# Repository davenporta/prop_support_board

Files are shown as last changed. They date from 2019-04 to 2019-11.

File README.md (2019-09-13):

# Prop Support Board
Michigan Aeronautial Science Association

Alex Davenport

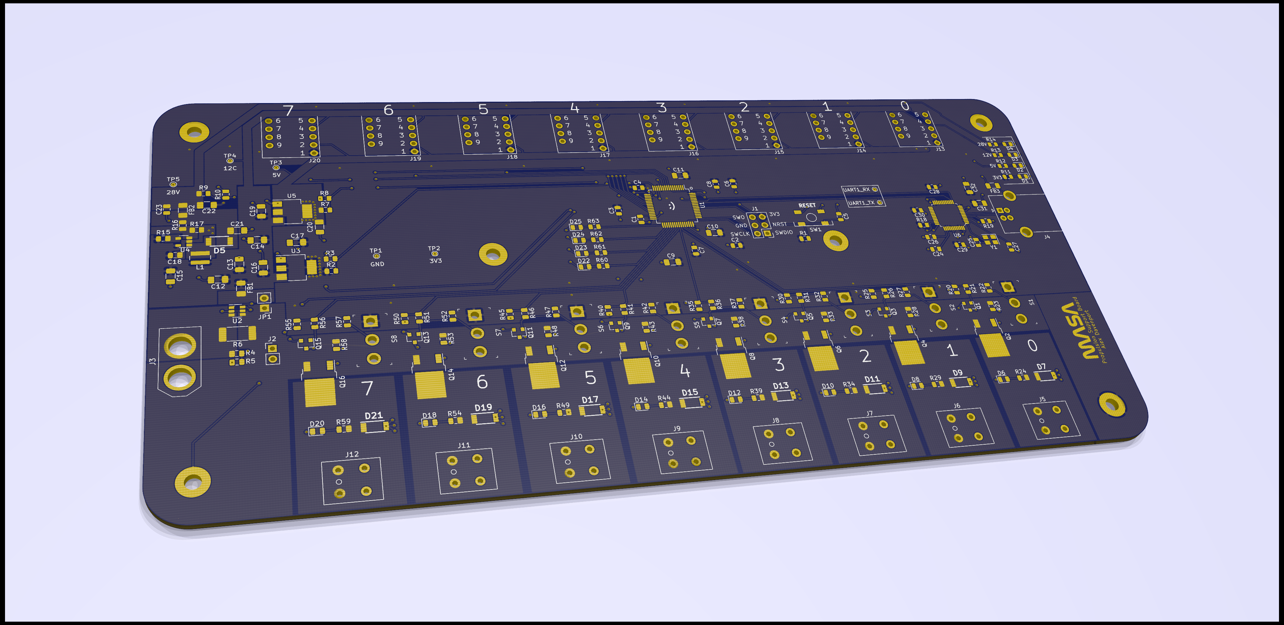
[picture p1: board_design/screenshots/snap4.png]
shiny


### Capabilities
* 8x 12V Solenoid Valve Channels
* 8x Configurable Sensor Channels

### Sensor Channels
* Analog signal out to MCU's integrated ADC
* 3.3V, 5V, 12V, and 28V supply
* Asymmetrical 9-pin header connector
* Configurable with 6 types of sensor conditioning "daughter" boards

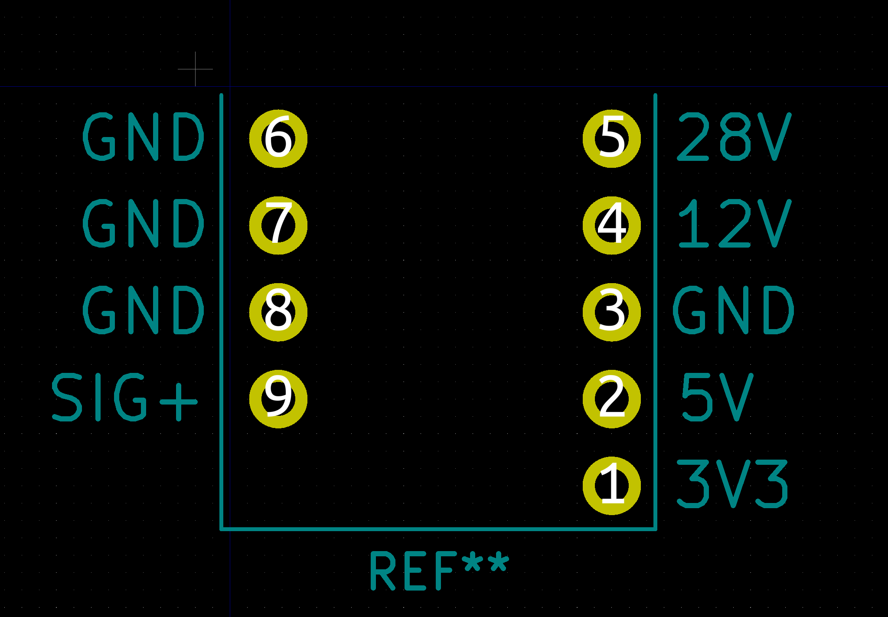
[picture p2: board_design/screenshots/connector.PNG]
asymmetrical!


### Available Sensor Boards
* 3-wire Pressure Transducer w/ configurable excitation
* 4-wire Pressure Transducer w/ configurable excitation (WIP)
* T or K-type Thermocouples
* Load Cells
* RTDs (WIP)
* Capacitive Level Sensor (WIP)

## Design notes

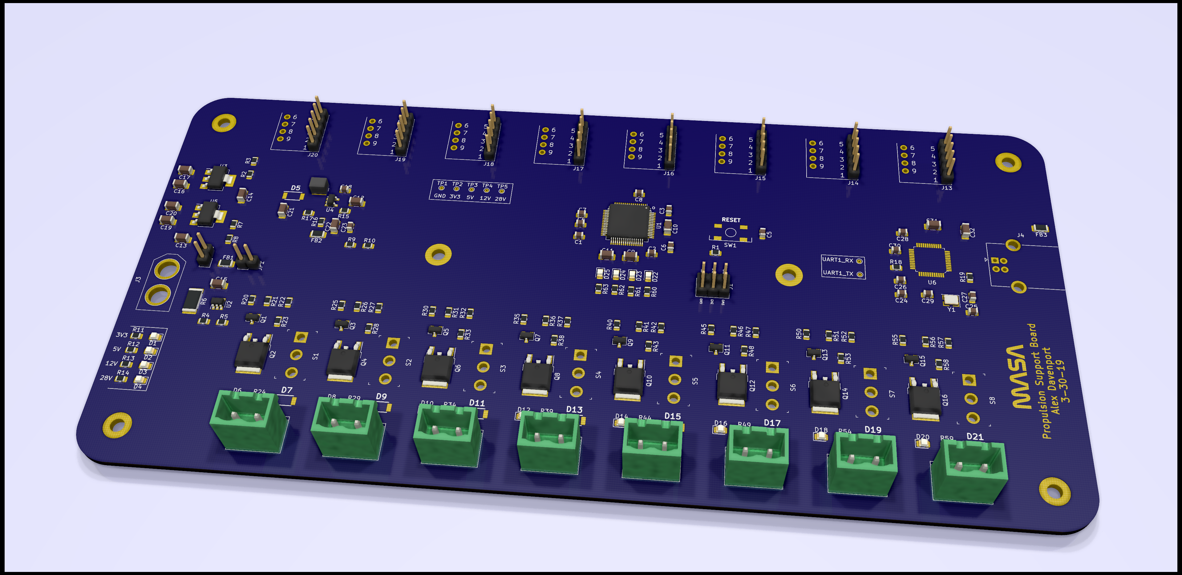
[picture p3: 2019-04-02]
board_design/screenshots/snap2.png

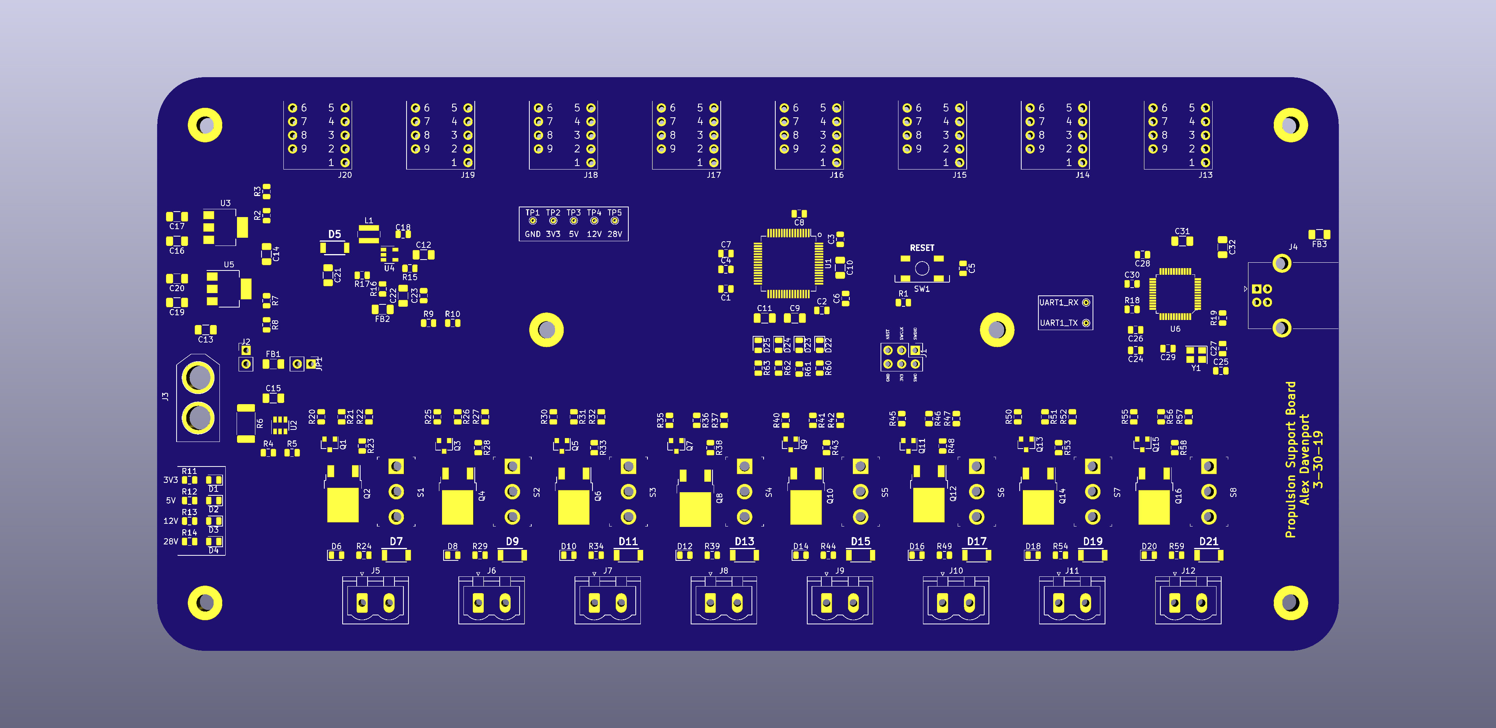
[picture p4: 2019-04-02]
board_design/screenshots/snap.png

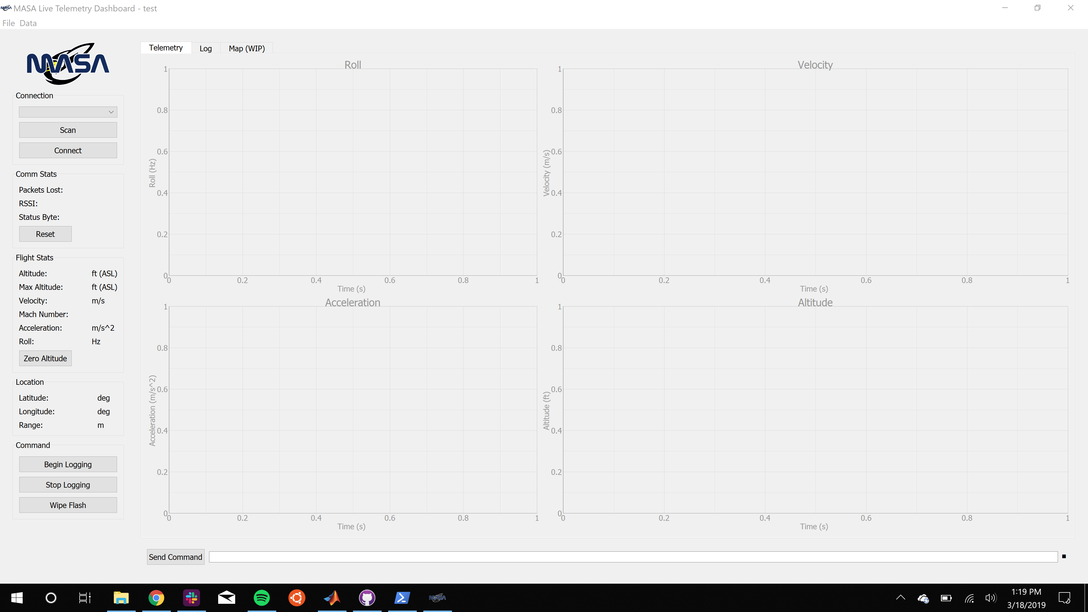
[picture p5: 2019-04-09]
gui/screenshot.png

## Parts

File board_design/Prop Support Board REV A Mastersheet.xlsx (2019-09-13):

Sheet: Pin Budget
ADC |  |  | GPIO
channel | pin | adc channel | channel | pin
ebatt | PA0 | ADC1_IN0 | en_vlv0 | PA11
ibus | PA1 | ADC1_IN1 | en_vlv1 | PA10
e3v3 | PA2 | ADC1_IN2 | en_vlv2 | PA9
e5v | PA3 | ADC1_IN3 | en_vlv3 | PA8
e28v | PA4 | ADC1_IN4 | en_vlv4 | PC9
sig0 | PA5 | ADC1_IN5 | en_vlv5 | PC8
sig1 | PA6 | ADC1_IN6 | en_vlv6 | PC7
sig2 | PA7 | ADC1_IN7 | en_vlv7 | PC6
sig3 | PB0 | ADC1_IN8 | LED_0 | PB12
sig4 | PB1 | ADC1_IN9 | LED_1 | PB13
sig5 | PC0 | ADC1_IN10 | LED_2 | PB14
sig6 | PC1 | ADC1_IN11 | LED_3 | PB15
sig7 | PC2 | ADC1_IN12

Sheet: Bill of Materials
Source: | C:\Users\alexh\OneDrive\Desktop\masa\prop_support_board\prop_support\prop_support.sch
Date: | 2019-03-30 15:33
Tool: | Eeschema (5.1.0)-1
Generator: | C:\Program Files\KiCad\bin\scripting\plugins/bom_csv_grouped_by_value.py
Component Count: | 183
Collated Components:
Item | Qty | Reference(s) | Value | LibPart | Footprint
1 | 2 | C1, C18 | 4u7 | Device:C | Capacitor_SMD:C_0805_2012Metric
2 | 13 | C2, C3, C4, C5, C6, C7, C8, C23, C24, C26, C28, C29, C30 | 100n | Device:C | Capacitor_SMD:C_0805_2012Metric
3 | 13 | C9, C10, C11, C12, C13, C14, C15, C16, C17, C19, C20, C21, C22 | 10u | Device:C | Capacitor_SMD:C_1206_3216Metric
4 | 2 | C25, C27 | 18p | Device:C | Capacitor_SMD:C_0805_2012Metric
5 | 2 | C31, C32 | 1u | Device:C | Capacitor_SMD:C_1206_3216Metric
6 | 16 | D1, D2, D3, D4, D6, D8, D10, D12, D14, D16, D18, D20, D22, D23, D24, D25 | LED | Device:LED | LED_SMD:LED_0805_2012Metric
7 | 1 | D5 | D_Schottky | Device:D_Schottky | davenport_kicad_footprints:SODFL4725X110N
8 | 8 | D7, D9, D11, D13, D15, D17, D19, D21 | D | Device:D | davenport_kicad_footprints:SODFL4725X110N
9 | 3 | FB1, FB2, FB3 | Ferrite_Bead | Device:Ferrite_Bead | Resistor_SMD:R_1206_3216Metric
10 | 6 | H1, H2, H3, H4, H5, H6 | MountingHole_Pad | Mechanical:MountingHole_Pad | MountingHole:MountingHole_3.2mm_M3_Pad
11 | 1 | J1 | Conn_02x03_Counter_Clockwise | Connector_Generic:Conn_02x03_Counter_Clockwise | Connector_PinHeader_1.00mm:PinHeader_2x03_P1.00mm_Vertical
12 | 1 | J2 | GS2 | Device:Jumper | Connector_PinHeader_1.00mm:PinHeader_1x02_P1.00mm_Vertical
13 | 1 | J3 | XT-60_female | davenport-kicad:XT-60_female | davenport_kicad_footprints:XT60
14 | 1 | J4 | USB_B | Connector:USB_B | Connector_USB:USB_B_OST_USB-B1HSxx_Horizontal
15 | 8 | J5, J6, J7, J8, J9, J10, J11, J12 | Screw_Terminal_01x02 | Connector:Screw_Terminal_01x02 | Connector_Phoenix_MSTB:PhoenixContact_MSTBVA_2,5_2-G_1x02_P5.00mm_Vertical
16 | 8 | J13, J14, J15, J16, J17, J18, J19, J20 | Conn_01x09_Female | Connector:Conn_01x09_Female | davenport_kicad_footprints:DaughterBoardConnector
17 | 1 | JP1 | Jumper | Device:Jumper | Connector_PinHeader_1.00mm:PinHeader_1x02_P1.00mm_Vertical
18 | 1 | L1 | 10uH | Device:L | Inductor_SMD:L_Wuerth_MAPI-4030
19 | 8 | Q1, Q3, Q5, Q7, Q9, Q11, Q13, Q15 | MMBT3904 | Transistor_BJT:MMBT3904 | Package_TO_SOT_SMD:SOT-23
20 | 8 | Q2, Q4, Q6, Q8, Q10, Q12, Q14, Q16 | Q_PMOS_GDS | Device:Q_PMOS_GDS | Package_TO_SOT_SMD:TO-252-2
21 | 49 | R1, R2, R3, R7, R8, R10, R11, R12, R18, R20, R21, R22, R23, R24, R25, R26, R27, R28, R29, R30, R31, R32, R33, R34, R35, R36, R37, R38, R39, R40, R41, R42, R43, R44, R45, R46, R47, R48, R49, R50, R51, R52, R53, R54, R55, R56, R57, R58, R59 | 1k | Device:R | Resistor_SMD:R_0805_2012Metric
22 | 4 | R4, R9, R13, R14 | 10k | Device:R | Resistor_SMD:R_0805_2012Metric
23 | 1 | R5 | 3k3 | Device:R | Resistor_SMD:R_0805_2012Metric
24 | 1 | R6 | 1m | Device:R | Resistor_SMD:R_2512_6332Metric
25 | 1 | R15 | 121k | Device:R | Resistor_SMD:R_0805_2012Metric
26 | 1 | R16 | 283k | Device:R | Resistor_SMD:R_0805_2012Metric
27 | 1 | R17 | 13k3 | Device:R | Resistor_SMD:R_0805_2012Metric
28 | 1 | R19 | 12k1% | Device:R | Resistor_SMD:R_0805_2012Metric
29 | 4 | R60, R61, R62, R63 | 220 | Device:R | Resistor_SMD:R_0805_2012Metric
30 | 8 | S1, S2, S3, S4, S5, S6, S7, S8 | 100SP3T1B1M2QE | davenport-kicad:100SP3T1B1M2QE | digikey-footprints:Toggle_Switch_100SP1T1B4M2QE
31 | 1 | SW1 | SW_Push | Switch:SW_Push | davenport_kicad_footprints:SKQGADE010
32 | 1 | U1 | STM32F446RETx | MCU_ST_STM32F4:STM32F446RETx | Package_QFP:LQFP-64_10x10mm_P0.5mm
33 | 1 | U2 | INA181 | Amplifier_Current:INA181 | Package_TO_SOT_SMD:SOT-23-6
34 | 1 | U3 | LM1117-3.3 | Regulator_Linear:LM1117-3.3 | Package_TO_SOT_SMD:SOT-223-3_TabPin2
35 | 1 | U4 | LT1930 | davenport-kicad:LT1930 | Package_TO_SOT_SMD:SOT-23-5
36 | 1 | U5 | LM1117-5.0 | Regulator_Linear:LM1117-5.0 | Package_TO_SOT_SMD:SOT-223-3_TabPin2
37 | 1 | U6 | FT232H | Interface_USB:FT232H | digikey-footprints:LQFP-48_7x7mm
38 | 1 | Y1 | CX3225CA | Device:Crystal_GND24 | Crystal:Crystal_SMD_3225-4Pin_3.2x2.5mm

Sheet: Calculations
 |  |  |  |  |  |  |  | Resistors
Voltage Divider |  |  |  |  |  |  |  | 100
Vin | R1 | R2 | Vout |  |  |  |  | 200
5 | 10000 | 200 | 0.09803921569 |  |  |  |  | 1000
 |  |  |  |  |  |  |  | 3300
 |  |  |  |  |  |  |  | 10000
Trace Calculator |  | Internal |  |  |  |  |  | 5000
Current |  |  | 2 | A | Trace Calc constants
Thickness |  |  | 1 | oz |  | External | Internal
Length |  |  | 1000 | mil | k | 0.048 | 0.024
Ambient Temperature |  |  | 25 | C | b | 0.44 | 0.44
Temperature Rise |  |  | 10 | C | c | 0.725 | 0.725
Area |  |  | 110.28 | mil^2
Width |  |  | 80.03 | mils
Resistance |  |  |  | ohm
Voltage Drop |  |  |  | V
Power Loss |  |  |  | W

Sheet: To Do
To do
clock configuration
fix trace calc
rev TC board

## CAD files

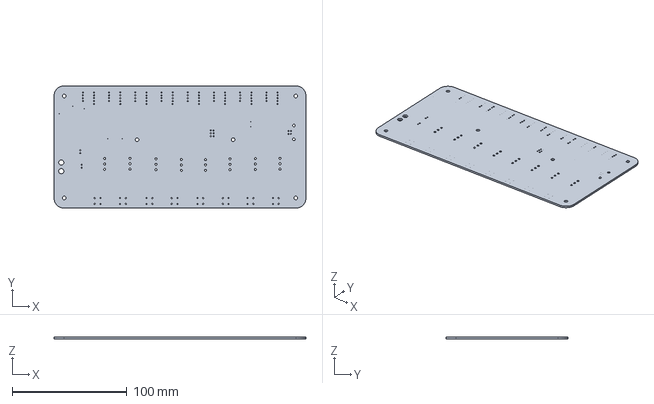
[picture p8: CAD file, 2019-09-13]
board_design/mechanical/psb_pcb.iges
219.7 x 106.7 x 1.60 mm

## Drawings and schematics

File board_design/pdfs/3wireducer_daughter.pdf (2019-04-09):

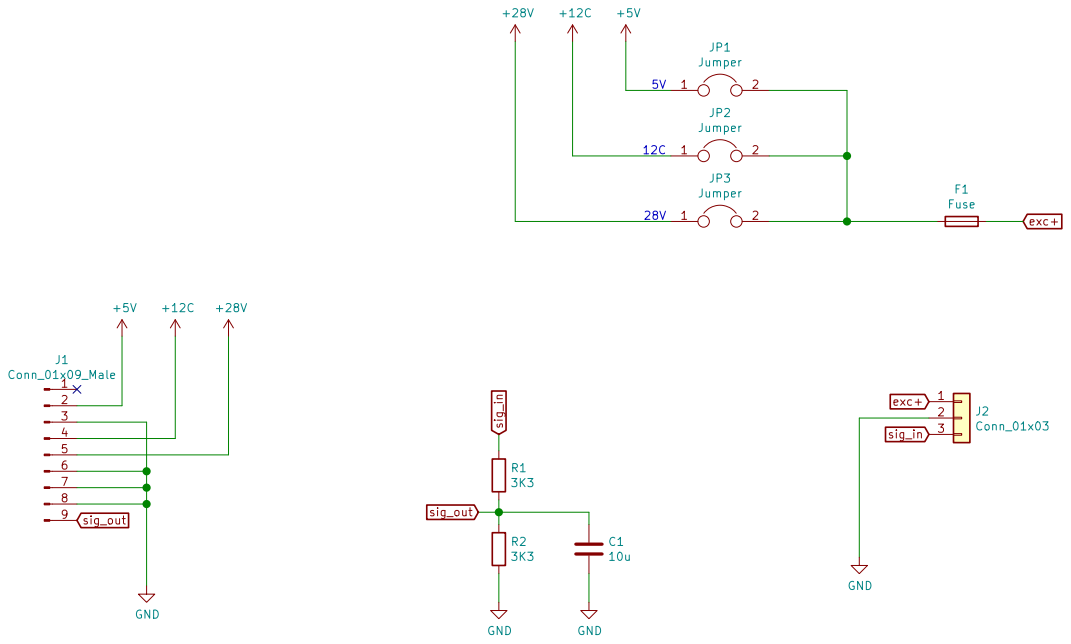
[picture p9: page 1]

Alex Davenport
File: 3wireducer_daughter.sch Sheet: / MASA

Id: 1/1 Title: 3-Wire Ducer Daughter Board

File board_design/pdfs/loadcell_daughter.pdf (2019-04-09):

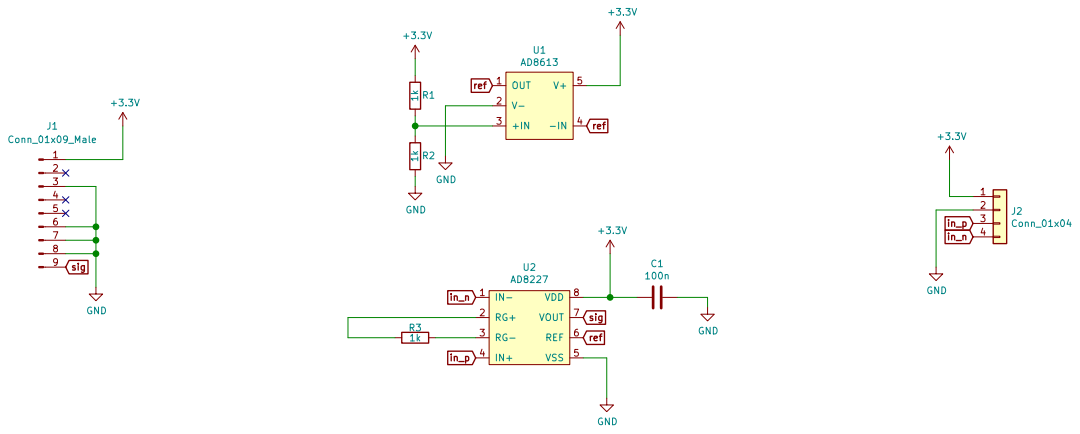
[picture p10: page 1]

Alex Davenport
File: loadcell_daughter.sch Sheet: / MASA

Id: 1/1 Title: Load Cell Daughter Board

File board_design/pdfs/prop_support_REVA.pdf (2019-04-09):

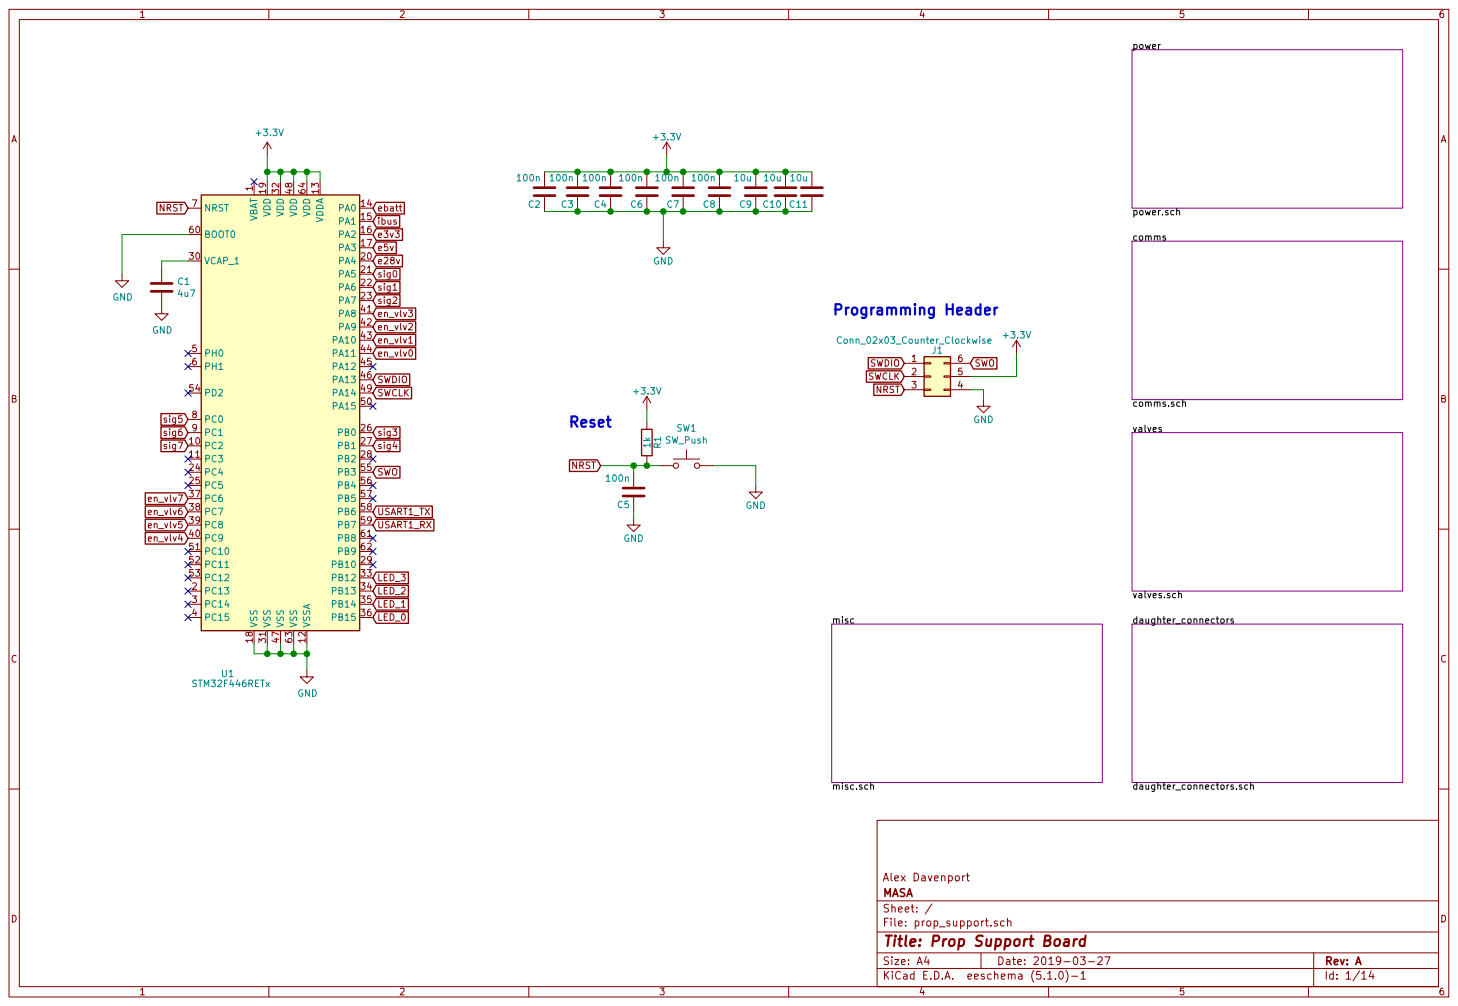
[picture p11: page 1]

1 VCAP_1 30 VDD 19 VDD 32 VDD 48 VDD 64 VDDA 13 VSS 18 VSS 31 VSS 47 VSS 63 VSSA 12 U1 STM32F446RETx

Alex Davenport
File: prop_support.sch Sheet: / MASA

Id: 1/14 Title: Prop Support Board

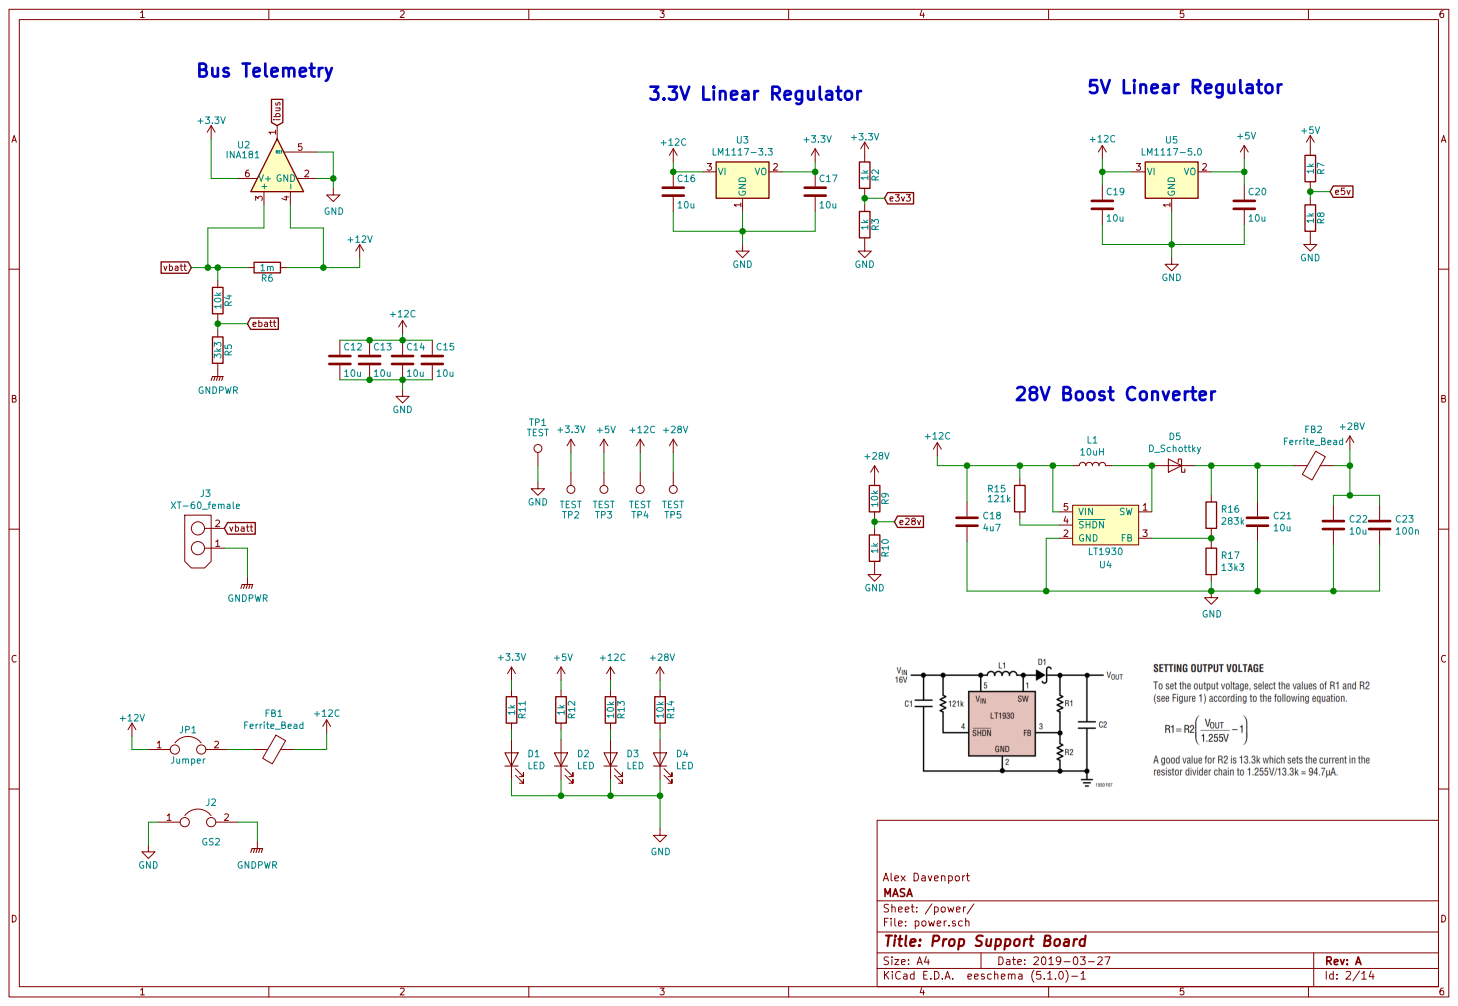
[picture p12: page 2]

vbatt GNDPWR Bus Telemetry

File: power.sch
Id: 2/14 Title: Prop Support Board

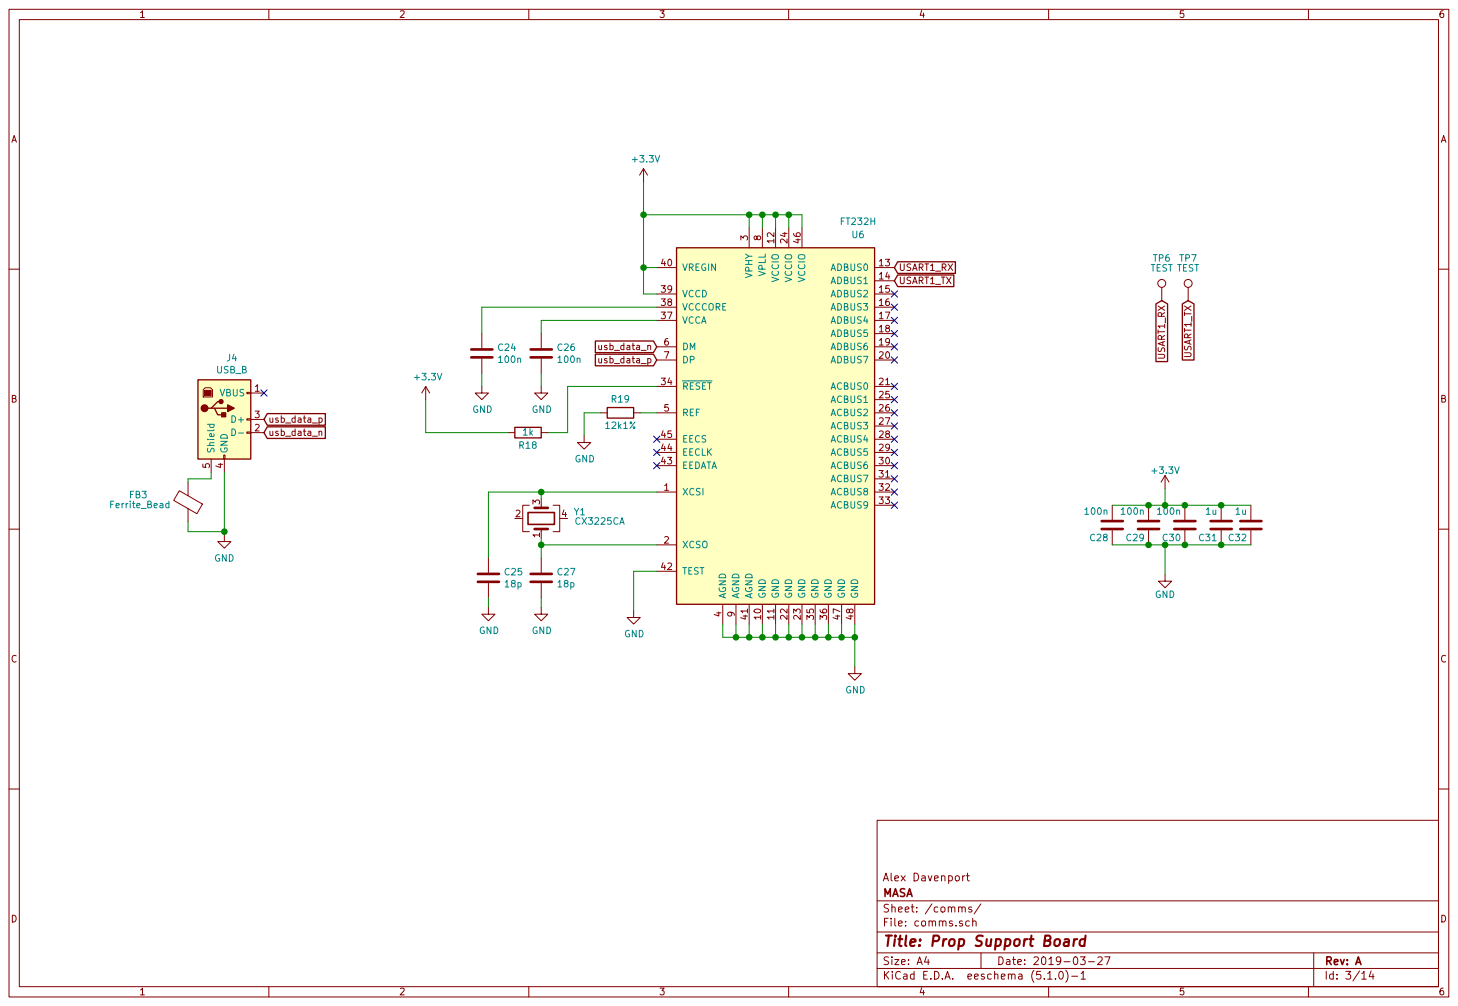
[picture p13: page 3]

4 VREGIN 40 AGND 41 TEST 42 EEDATA 43 EECLK 44 EECS 45 VCCIO 46 GND 47 GND 48 REF 5 DM 6 DP 7 VPLL

3 ACBUS6 30 ACBUS7 31 ACBUS8 32 ACBUS9 33 RESET 34 GND 35 GND 36 VCCA 37 VCCCORE 38 VCCD 39 AGND

File: comms.sch Sheet: /comms/ MASA

Id: 3/14 Title: Prop Support Board

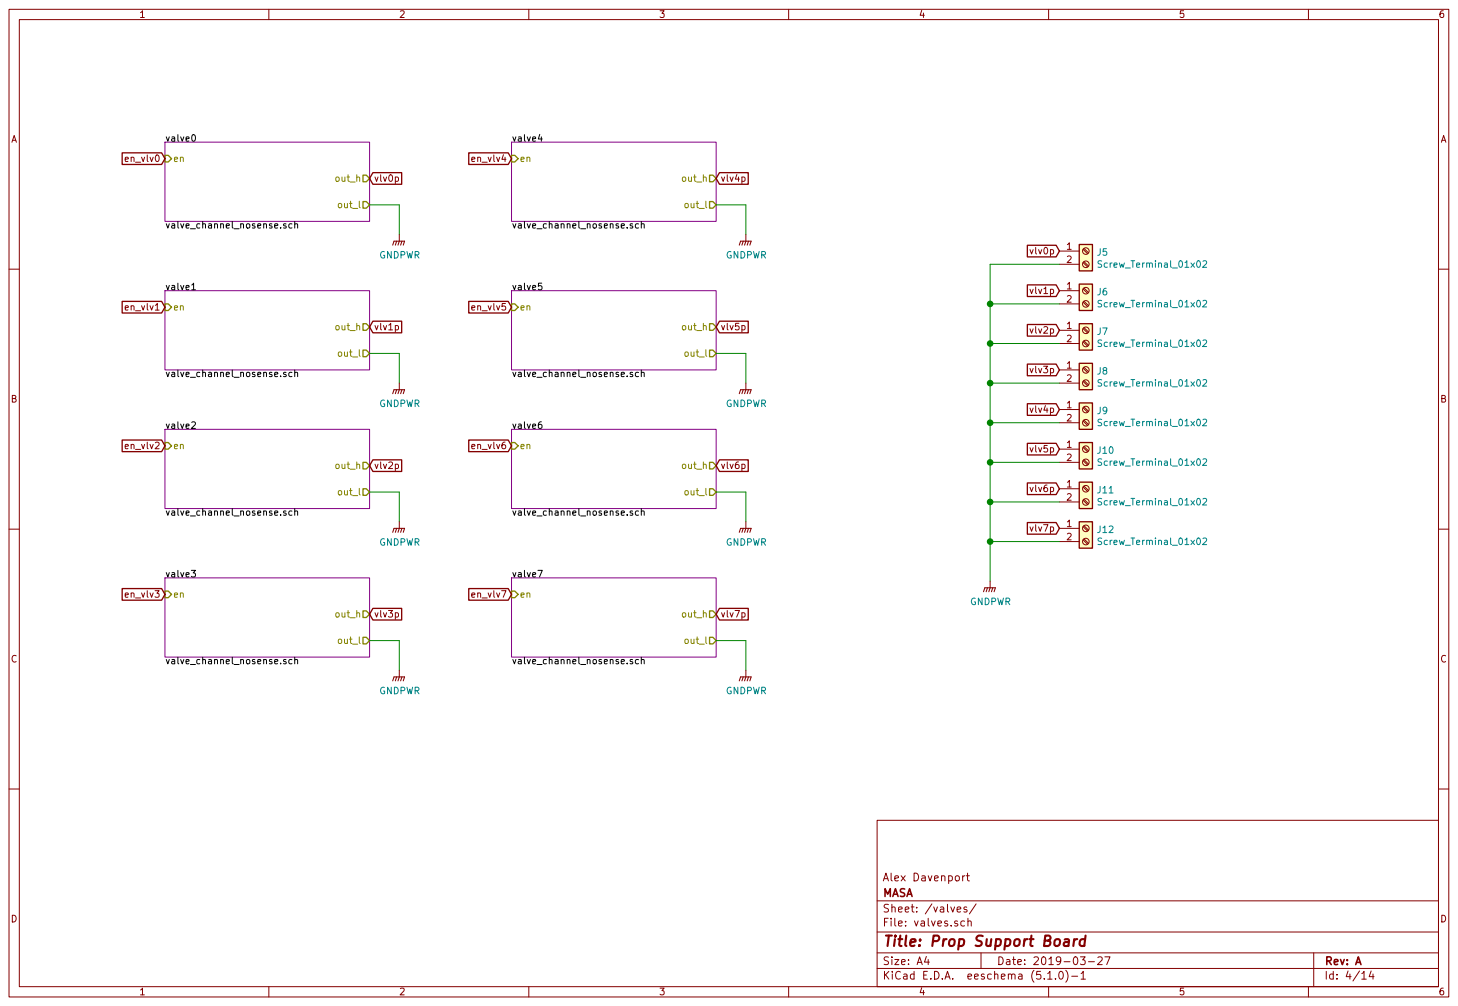
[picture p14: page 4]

out_l GNDPWR GNDPWR GNDPWR GNDPWR

Alex Davenport
File: valves.sch Sheet: /valves/ MASA

Id: 4/14 Title: Prop Support Board

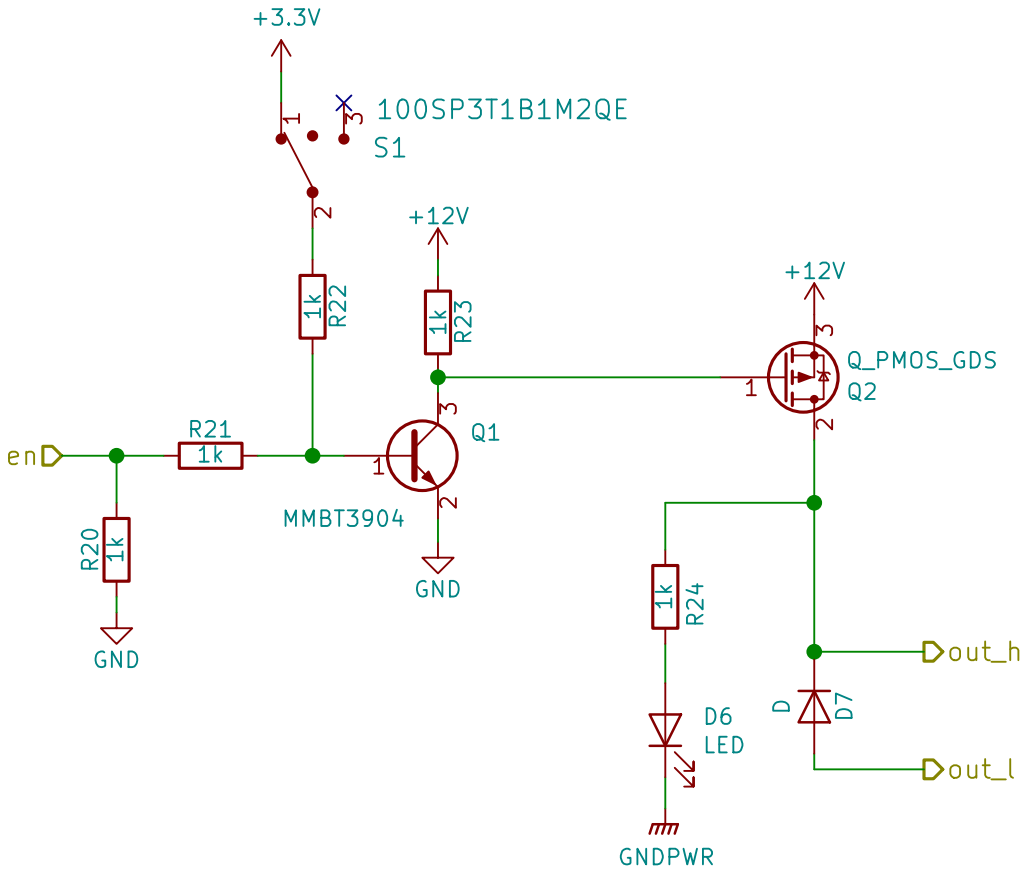
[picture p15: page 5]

Alex Davenport
File: valve_channel_nosense.sch Sheet: /valves/valve0/ MASA

Id: 5/14 Title: Prop Support Board

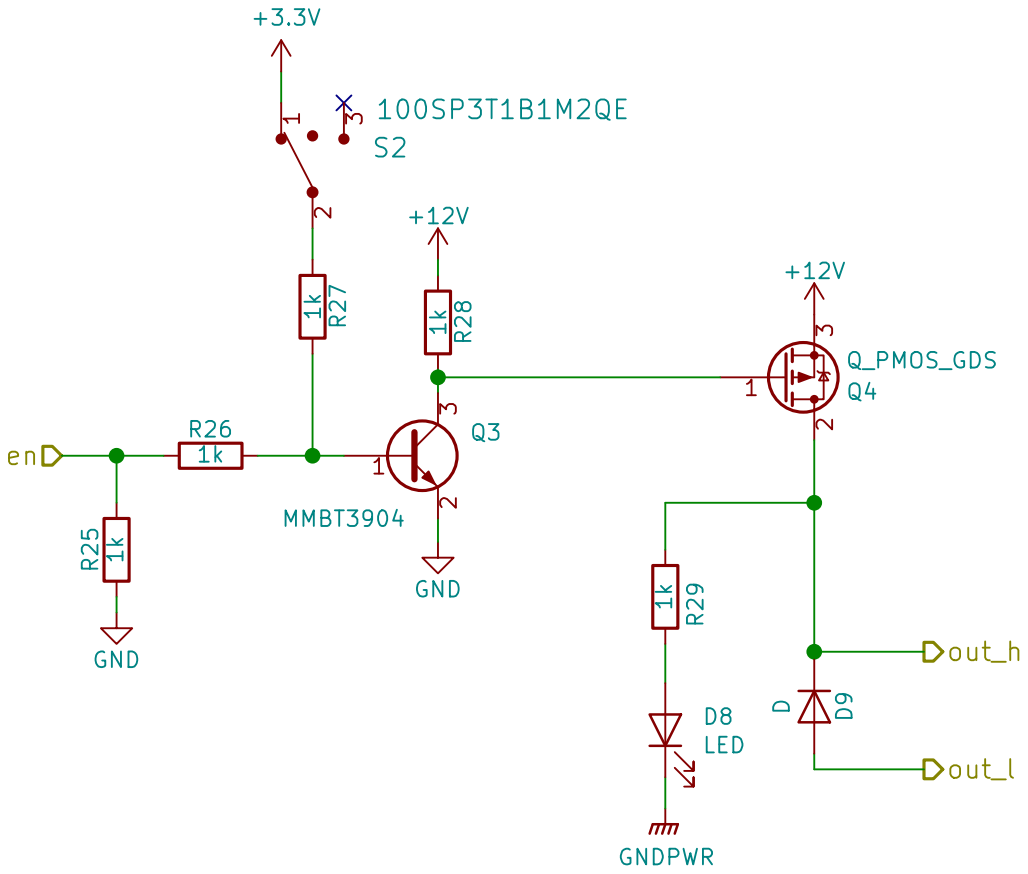
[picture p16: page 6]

Alex Davenport
File: valve_channel_nosense.sch Sheet: /valves/valve1/ MASA

Id: 6/14 Title: Prop Support Board

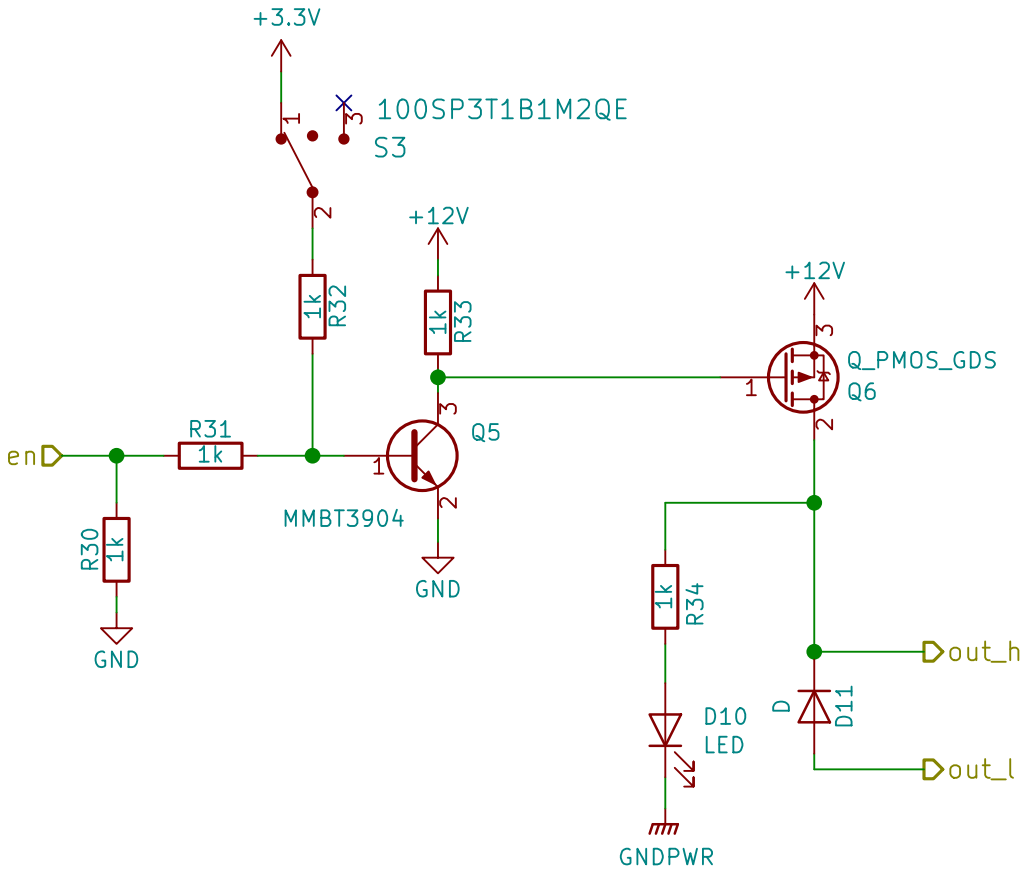
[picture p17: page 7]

Alex Davenport
File: valve_channel_nosense.sch Sheet: /valves/valve2/ MASA

Id: 7/14 Title: Prop Support Board

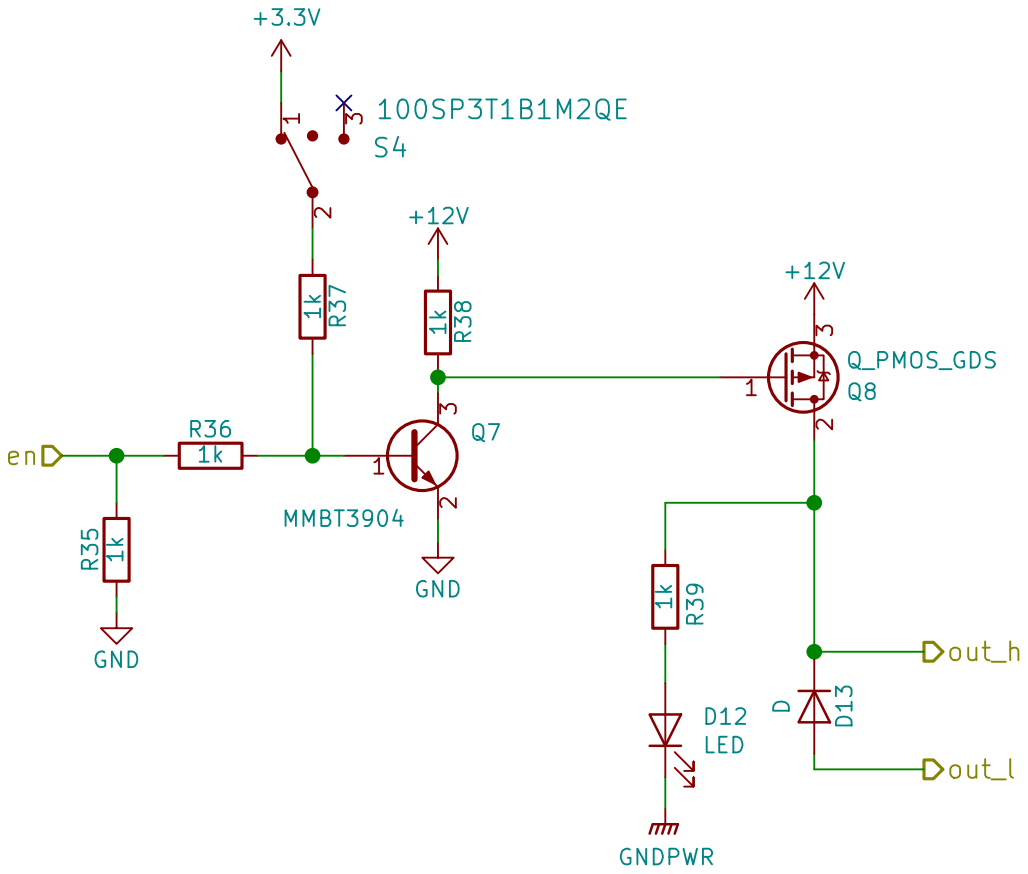
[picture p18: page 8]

Alex Davenport
File: valve_channel_nosense.sch Sheet: /valves/valve3/ MASA

Id: 8/14 Title: Prop Support Board

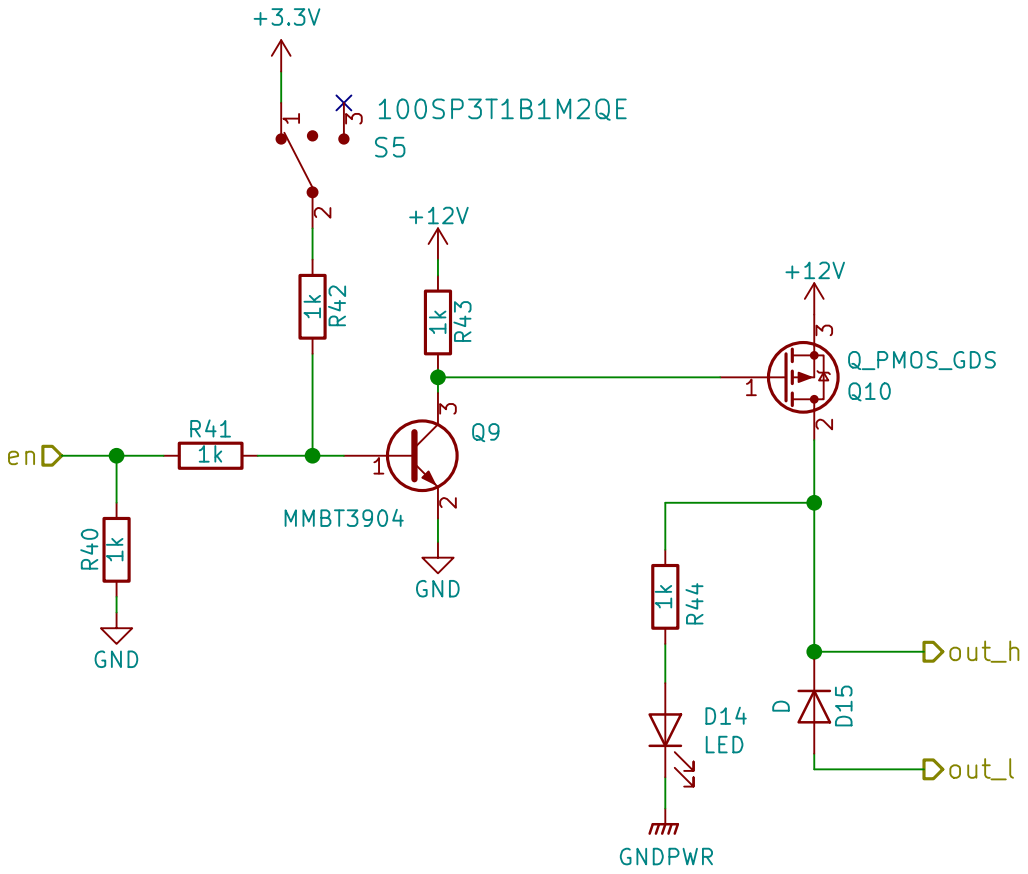
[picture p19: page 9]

Alex Davenport
File: valve_channel_nosense.sch Sheet: /valves/valve4/ MASA

Id: 9/14 Title: Prop Support Board

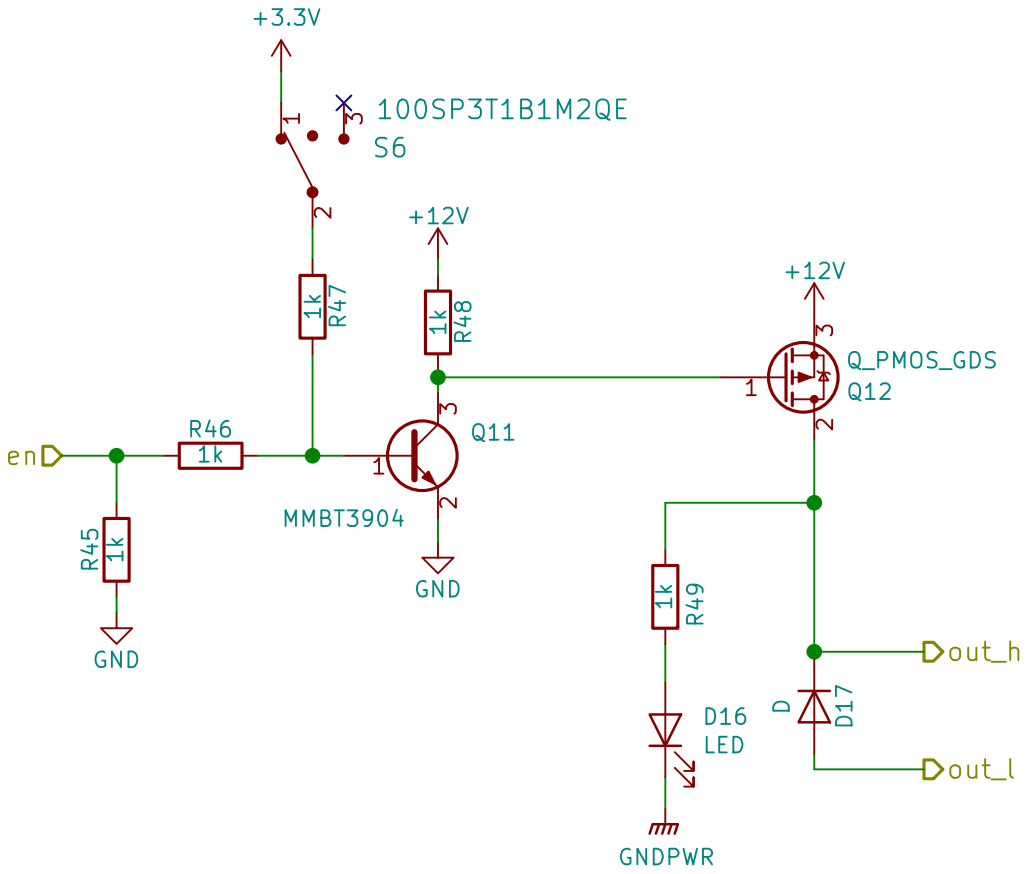
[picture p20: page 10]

Alex Davenport
File: valve_channel_nosense.sch Sheet: /valves/valve5/ MASA

Id: 10/14 Title: Prop Support Board


Alex Davenport
File: valve_channel_nosense.sch Sheet: /valves/valve6/ MASA

Id: 11/14 Title: Prop Support Board


Alex Davenport
File: valve_channel_nosense.sch Sheet: /valves/valve7/ MASA

Id: 12/14 Title: Prop Support Board


File: daughter_connectors.sch
Id: 13/14 Title: Prop Support Board


Alex Davenport
File: misc.sch Sheet: /misc/ MASA

Id: 14/14 Title: Prop Support Board

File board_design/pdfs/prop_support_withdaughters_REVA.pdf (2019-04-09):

BOOT0 60 NRST 7 | PA0 14 PA1 15 PA10 43 PA11 44 PA12 45 PA13 46 PA14 49 PA15 50 PA2 16 PA3 17 PA4 20 PA5 21 PA6 22 PA7 23 PA8 41 PA9 42 PB0 26 PB1 27 PB10 29 PB12 33 PB13 34 PB14 35 PB15 36 PB2 28 PB3 55 PB4 56 PB5 57 PB6 58 PB7 59 PB8 61 PB9 62 PC0 8 PC1 9 PC10 51 PC11 52 PC12 53 PC13 2 PC14 3 PC15 4 PC2 10 PC3 11 PC4 24 PC5 25 PC6 37 PC7 38 PC8 39 PC9 40 PD2 54 PH0 5 PH1 6 | VBAT

# power power.sch


1 VCAP_1 30 VDD 19 VDD 32 VDD 48 VDD 64 VDDA 13 VSS 18 VSS 31 VSS 47 VSS 63 VSSA 12 U1 STM32F446RETx
NRST

Alex Davenport
File: prop_support.sch Sheet: / MASA

Id: 1/14 Title: Prop Support Board

3.3V Linear Regulator | 5V Linear Regulator
ebatt +3.3V | ibus


vbatt GNDPWR Bus Telemetry

LED ¹⁰k R¹⁴ GND

File: power.sch
Id: 2/14 Title: Prop Support Board


4 VREGIN 40 AGND 41 TEST 42 EEDATA 43 EECLK 44 EECS 45 VCCIO 46 GND 47 GND 48 REF 5 DM 6 DP 7 VPLL

3 ACBUS6 30 ACBUS7 31 ACBUS8 32 ACBUS9 33 RESET 34 GND 35 GND 36 VCCA 37 VCCCORE 38 VCCD 39 AGND

File: comms.sch Sheet: /comms/ MASA

Id: 3/14 Title: Prop Support Board

D Date: 2019-03-27 KiCad E.D.A. eeschema (5.1.0)-1 Size: A4; Rev: A; valve0; valve_channel_nosense.sch; out_h; out_l valve1; out_l valve2; out_l valve3; out_l; valve4; out_l valve5; out_l valve6; out_l valve7; vlv0p; en_vlv0; vlv1p; vlv2p; vlv3p; GNDPWR GNDPWR GNDPWR GNDPWR; vlv4p; vlv5p; vlv6p; vlv7p; en_vlv1; en_vlv2; en_vlv3; en_vlv4; en_vlv5; en_vlv6; en_vlv7; J5Screw_Terminal_01x02; J6Screw_Terminal_01x02; J7Screw_Terminal_01x02; J8Screw_Terminal_01x02; J9Screw_Terminal_01x02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

out_l GNDPWR GNDPWR GNDPWR GNDPWR

Alex Davenport
File: valves.sch Sheet: /valves/ MASA

Id: 4/14 Title: Prop Support Board

D Date: 2019-03-27 KiCad E.D.A. eeschema (5.1.0)-1 Size: A4; Rev: A; +12V GND R²⁰ ¹k; R²³ ¹k GND; out_h; out_l ¹; 2 3 Q2 Q_PMOS_GDS GNDPWR; 100SP3T1B1M2QE R²² ¹k; 2 3 Q1 MMBT3904 R241k D6; LED

Alex Davenport
File: valve_channel_nosense.sch Sheet: /valves/valve0/ MASA

Id: 5/14 Title: Prop Support Board

D Date: 2019-03-27 KiCad E.D.A. eeschema (5.1.0)-1 Size: A4; Rev: A; +12V GND R²⁵ ¹k; R²⁸ ¹k GND; out_h; out_l ¹; 2 3 Q4 Q_PMOS_GDS GNDPWR; 100SP3T1B1M2QE R²⁷ ¹k; 2 3 Q3 MMBT3904 R291k D8; LED

Alex Davenport
File: valve_channel_nosense.sch Sheet: /valves/valve1/ MASA

Id: 6/14 Title: Prop Support Board

D Date: 2019-03-27 KiCad E.D.A. eeschema (5.1.0)-1 Size: A4; Rev: A; +12V GND R³⁰ ¹k; R³³ ¹k GND; out_h; out_l ¹; 2 3 Q6 Q_PMOS_GDS GNDPWR; 100SP3T1B1M2QE R³² ¹k; 2 3 Q5 MMBT3904 R341k D10; LED; D¹¹ D

Alex Davenport
File: valve_channel_nosense.sch Sheet: /valves/valve2/ MASA

Id: 7/14 Title: Prop Support Board

D Date: 2019-03-27 KiCad E.D.A. eeschema (5.1.0)-1 Size: A4; Rev: A; +12V GND R³⁵ ¹k; R³⁸ ¹k GND; out_h; out_l ¹; 2 3 Q8 Q_PMOS_GDS GNDPWR; 100SP3T1B1M2QE R³⁷ ¹k; 2 3 Q7 MMBT3904 R391k D12; LED; D¹³ D

Alex Davenport
File: valve_channel_nosense.sch Sheet: /valves/valve3/ MASA

Id: 8/14 Title: Prop Support Board

D Date: 2019-03-27 KiCad E.D.A. eeschema (5.1.0)-1 Size: A4; Rev: A; +12V GND R⁴⁰ ¹k; R⁴³ ¹k GND; out_h; out_l ¹; 2 3 Q10 Q_PMOS_GDS GNDPWR; 100SP3T1B1M2QE R⁴² ¹k; 2 3 Q9 MMBT3904 R441k D14; LED; D¹⁵ D

Alex Davenport
File: valve_channel_nosense.sch Sheet: /valves/valve4/ MASA

Id: 9/14 Title: Prop Support Board

D Date: 2019-03-27 KiCad E.D.A. eeschema (5.1.0)-1 Size: A4; Rev: A; +12V GND R⁴⁵ ¹k; R⁴⁸ ¹k GND; out_h; out_l ¹; 2 3 Q12 Q_PMOS_GDS GNDPWR; 100SP3T1B1M2QE R⁴⁷ ¹k; 2 3 Q11 MMBT3904 R491k D16; LED; D¹⁷ D

Alex Davenport
File: valve_channel_nosense.sch Sheet: /valves/valve5/ MASA

Id: 10/14 Title: Prop Support Board

D Date: 2019-03-27 KiCad E.D.A. eeschema (5.1.0)-1 Size: A4; Rev: A; +12V GND R⁵⁰ ¹k; R⁵³ ¹k GND; out_h; out_l ¹; 2 3 Q14 Q_PMOS_GDS GNDPWR; 100SP3T1B1M2QE R⁵² ¹k; 2 3 Q13 MMBT3904 R541k D18; LED; D¹⁹ D

Alex Davenport
File: valve_channel_nosense.sch Sheet: /valves/valve6/ MASA

Id: 11/14 Title: Prop Support Board

D Date: 2019-03-27 KiCad E.D.A. eeschema (5.1.0)-1 Size: A4; Rev: A; +12V GND R⁵⁵ ¹k; R⁵⁸ ¹k GND; out_h; out_l ¹; 2 3 Q16 Q_PMOS_GDS GNDPWR; 100SP3T1B1M2QE R⁵⁷ ¹k; 2 3 Q15 MMBT3904 R591k D20; LED; D²¹ D

Alex Davenport
File: valve_channel_nosense.sch Sheet: /valves/valve7/ MASA

Id: 12/14 Title: Prop Support Board

+28V | +5V +3.3V 123456789
+28V | +5V +3.3V123456789
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

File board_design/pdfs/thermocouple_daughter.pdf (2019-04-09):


Alex Davenport
File: thermocouple_daughter.sch Sheet: / MASA

Id: 1/1 Title: T-Type Thermocouple Daughter Board







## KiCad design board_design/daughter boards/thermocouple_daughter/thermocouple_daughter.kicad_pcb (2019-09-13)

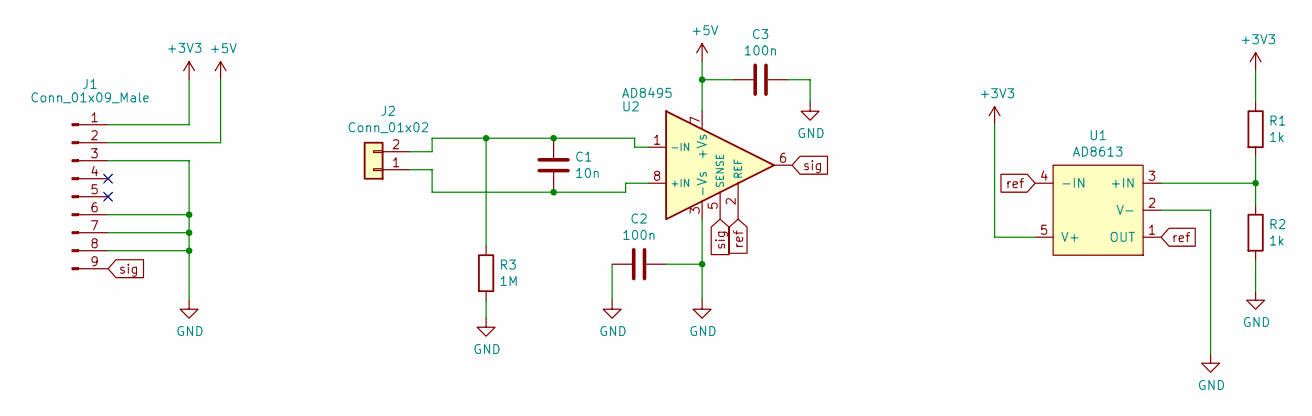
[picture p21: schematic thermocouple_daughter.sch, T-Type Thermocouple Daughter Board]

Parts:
C1: 10n; C_0805_2012Metric
C2, C3: 100n; C_0805_2012Metric
J1: Conn_01x09_Male; DaughterBoardConnector
J2: Conn_01x02; PCC-OST
R1, R2: 1k; R_0805_2012Metric
R3: 1M; R_0805_2012Metric
U1: AD8613; TSOT-23-5
U2: AD8495; MSOP-8_3x3mm_P0.65mm

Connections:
+3V3: J1.1, R1.1, U1.5 (V+)
+5V: C3.1, J1.2, U2.7 (+Vs)
GND: C2.1, C2.2, C3.2, J1.3, J1.6, J1.7, J1.8, R2.2, R3.2, U1.2 (V-), U2.3 (-Vs)
unnamed: C1.1, J2.2, R3.1, U2.1 (-IN)
unnamed: C1.2, J2.1, U2.8 (+IN)
unnamed: R1.2, R2.1, U1.3 (+IN)
unnamed: U1.1 (OUT), U1.4 (-IN), U2.2 (REF)
sig: J1.9, U2.5 (SENSE), U2.6

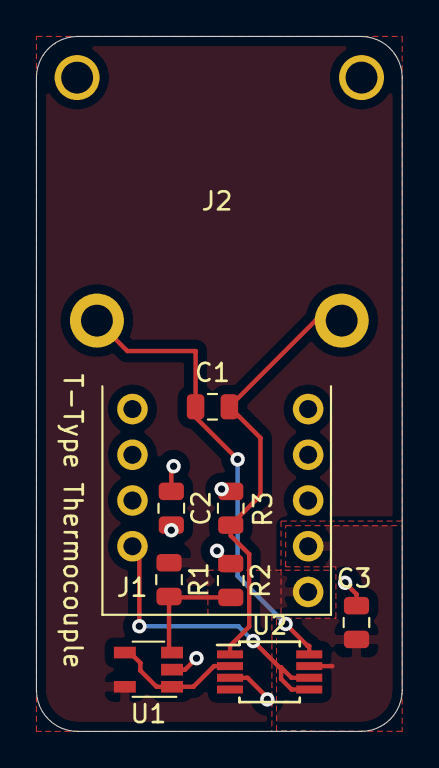
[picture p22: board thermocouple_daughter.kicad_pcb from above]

Board: 2 copper layers, 20.3 x 38.6 mm, 10 parts (0 on the bottom side), 8 nets.

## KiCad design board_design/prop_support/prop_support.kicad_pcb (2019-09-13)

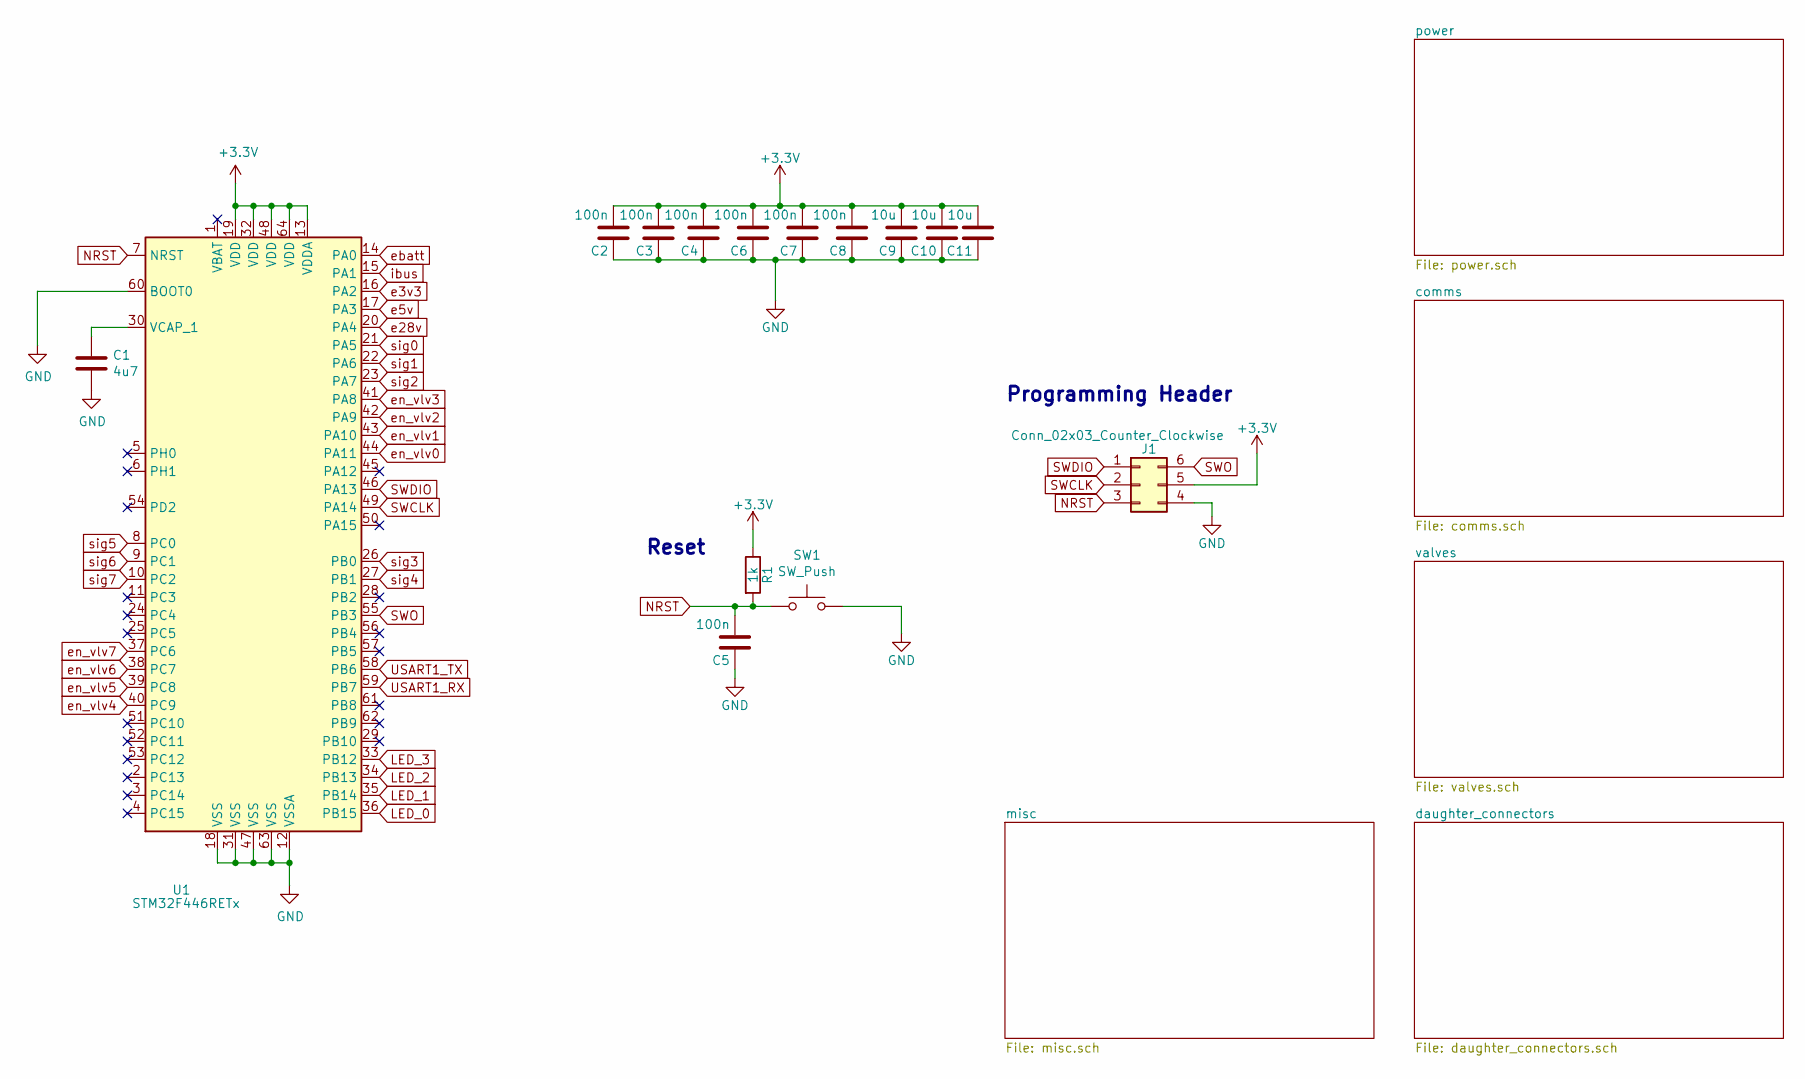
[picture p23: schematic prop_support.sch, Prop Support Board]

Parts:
C1: 4u7; C_0805_2012Metric
C2, C3, C4, C5, C6, C7, C8: 100n; C_0805_2012Metric
C9, C10, C11: 10u; C_1206_3216Metric
J1: Conn_02x03_Counter_Clockwise; PinHeader_2x03_P2.54mm_Vertical
R1: 1k; R_0805_2012Metric
SW1: SW_Push; SKQGADE010
U1: STM32F446RETx; LQFP-64_10x10mm_P0.5mm

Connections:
+3V3: C2.2, C3.2, C4.2, C6.2, C7.2, C8.2, C9.2, C10.2, C11.2, J1.5, R1.1, U1.13 (VDDA), U1.19 (VDD), U1.32 (VDD), U1.48 (VDD), U1.64 (VDD); also elsewhere on the board
GND: C1.2, C2.1, C3.1, C4.1, C5.1, C6.1, C7.1, C8.1, C9.1, C10.1, C11.1, J1.4, SW1.2, U1.12 (VSSA), U1.18 (VSS), U1.31 (VSS), U1.47 (VSS), U1.60 (BOOT0), U1.63 (VSS); also elsewhere on the board
LED_0: U1.36 (PB15); also elsewhere on the board
LED_1: U1.35 (PB14); also elsewhere on the board
LED_2: U1.34 (PB13); also elsewhere on the board
LED_3: U1.33 (PB12); also elsewhere on the board
NRST: C5.2, J1.3, R1.2, SW1.1, U1.7 (NRST)
unnamed: C1.1, U1.30 (VCAP_1)
SWCLK: J1.2, U1.49 (PA14)
SWDIO: J1.1, U1.46 (PA13)
SWO: J1.6, U1.55 (PB3)
USART1_RX: U1.59 (PB7); also elsewhere on the board
USART1_TX: U1.58 (PB6); also elsewhere on the board
e3v3: U1.16 (PA2); also elsewhere on the board
e5v: U1.17 (PA3); also elsewhere on the board
e28v: U1.20 (PA4); also elsewhere on the board
ebatt: U1.14 (PA0); also elsewhere on the board
en_vlv0: U1.44 (PA11); also elsewhere on the board
en_vlv1: U1.43 (PA10); also elsewhere on the board
en_vlv2: U1.42 (PA9); also elsewhere on the board
en_vlv3: U1.41 (PA8); also elsewhere on the board
en_vlv4: U1.40 (PC9); also elsewhere on the board
en_vlv5: U1.39 (PC8); also elsewhere on the board
en_vlv6: U1.38 (PC7); also elsewhere on the board
en_vlv7: U1.37 (PC6); also elsewhere on the board
ibus: U1.15 (PA1); also elsewhere on the board
sig0: U1.21 (PA5); also elsewhere on the board
sig1: U1.22 (PA6); also elsewhere on the board
sig2: U1.23 (PA7); also elsewhere on the board
sig3: U1.26 (PB0); also elsewhere on the board
sig4: U1.27 (PB1); also elsewhere on the board
sig5: U1.8 (PC0); also elsewhere on the board
sig6: U1.9 (PC1); also elsewhere on the board
sig7: U1.10 (PC2); also elsewhere on the board

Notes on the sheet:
Programming Header
Reset

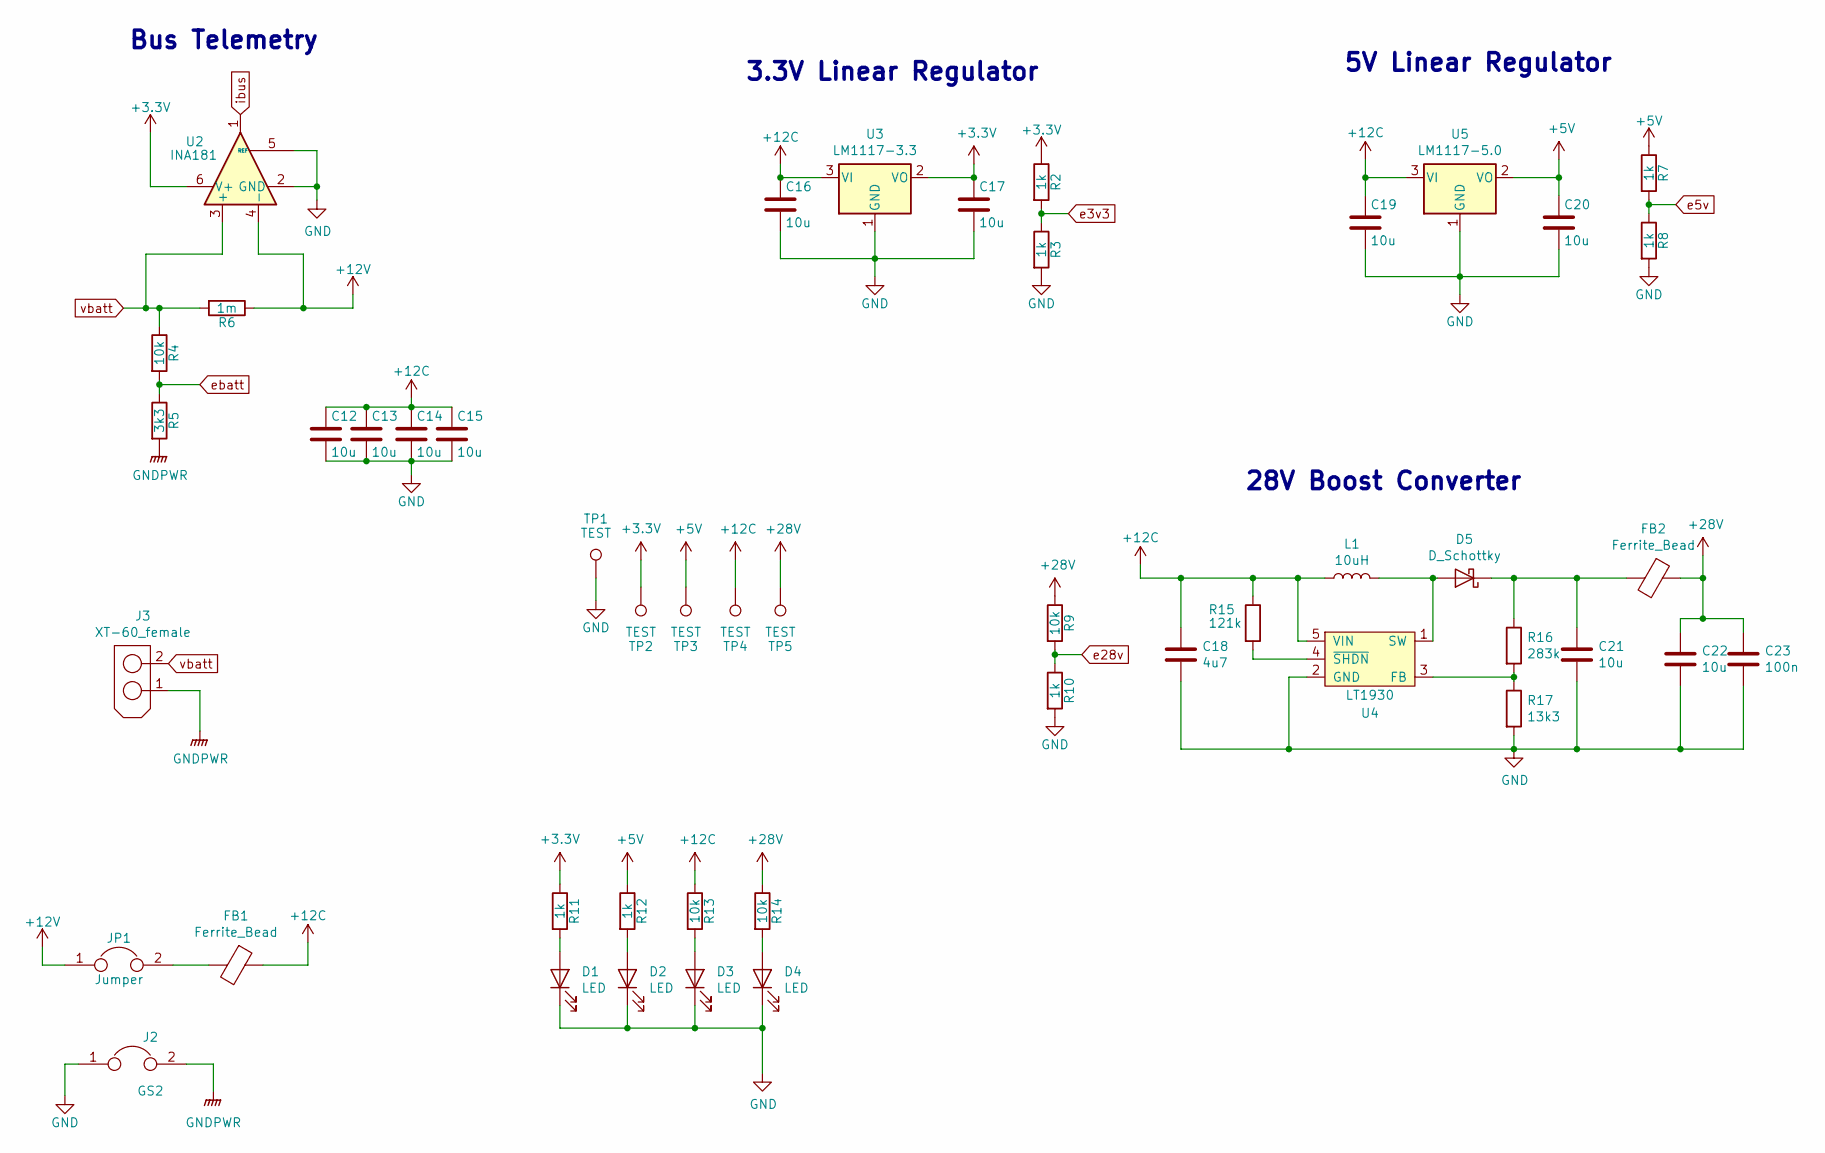
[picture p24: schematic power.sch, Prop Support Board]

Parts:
C12, C13, C14, C15, C16, C17, C19, C20, C21, C22: 10u; C_1206_3216Metric
C18: 4u7; C_0805_2012Metric
C23: 100n; C_0805_2012Metric
D1, D2, D3, D4: LED; LED_0805_2012Metric
D5: D_Schottky; SODFL4725X110N
FB1, FB2: Ferrite_Bead; R_1206_3216Metric
J2: GS2; PinHeader_1x02_P2.54mm_Vertical
J3: XT-60_female; XT60
JP1: Jumper; PinHeader_1x02_P2.54mm_Vertical
L1: 10uH; L_Wuerth_MAPI-4030
R2, R3, R7, R8, R10, R11, R12: 1k; R_0805_2012Metric
R4, R9, R13, R14: 10k; R_0805_2012Metric
R5: 3k3; R_0805_2012Metric
R6: 1m; R_2512_6332Metric
R15: 121k; R_0805_2012Metric
R16: 283k; R_0805_2012Metric
R17: 13k3; R_0805_2012Metric
TP1, TP2, TP3, TP4, TP5: TEST; TestPoint_THTPad_D1.0mm_Drill0.5mm
U2: INA181; SOT-23-6
U3: LM1117-3.3; SOT-223-3_TabPin2
U4: LT1930; SOT-23-5
U5: LM1117-5.0; SOT-223-3_TabPin2

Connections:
+3V3: C17.1, R2.1, R11.1, TP2.1, U2.6 (V+), U3.2 (VO); also elsewhere on the board
+5V: C20.1, R7.1, R12.1, TP3.1, U5.2 (VO); also elsewhere on the board
+12C: C12.1, C13.1, C14.1, C15.1, C16.1, C18.1, C19.1, FB1.1, L1.1, R13.1, R15.1, TP4.1, U3.3 (VI), U4.5 (VIN), U5.3 (VI); also elsewhere on the board
+12V: JP1.1, R6.1, U2.4 (-); also elsewhere on the board
+28V: C22.1, C23.1, FB2.1, R9.1, R14.1, TP5.1; also elsewhere on the board
GND: C12.2, C13.2, C14.2, C15.2, C16.2, C17.2, C18.2, C19.2, C20.2, C21.2, C22.2, C23.2, D1.1 (K), D2.1 (K), D3.1 (K), D4.1 (K), J2.1, R3.2, R8.2, R10.2, R17.2, TP1.1, U2.2 (GND), U2.5 (REF), U3.1 (GND), U4.2 (GND), U5.1 (GND); also elsewhere on the board
GNDPWR: J2.2, J3.1, R5.2; also elsewhere on the board
unnamed: C21.1, D5.1 (K), FB2.2, R16.1
unnamed: D1.2 (A), R11.2
unnamed: D2.2 (A), R12.2
unnamed: D3.2 (A), R13.2
unnamed: D4.2 (A), R14.2
unnamed: D5.2 (A), L1.2, U4.1 (SW)
unnamed: FB1.2, JP1.2
unnamed: R15.2, U4.4 (~SHDN~)
unnamed: R16.2, R17.1, U4.3 (FB)
e3v3: R2.2, R3.1; also elsewhere on the board
e5v: R7.2, R8.1; also elsewhere on the board
e28v: R9.2, R10.1; also elsewhere on the board
ebatt: R4.2, R5.1; also elsewhere on the board
ibus: U2.1; also elsewhere on the board
vbatt: J3.2, R4.1, R6.2, U2.3 (+)

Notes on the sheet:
28V Boost Converter
3.3V Linear Regulator
5V Linear Regulator
Bus Telemetry

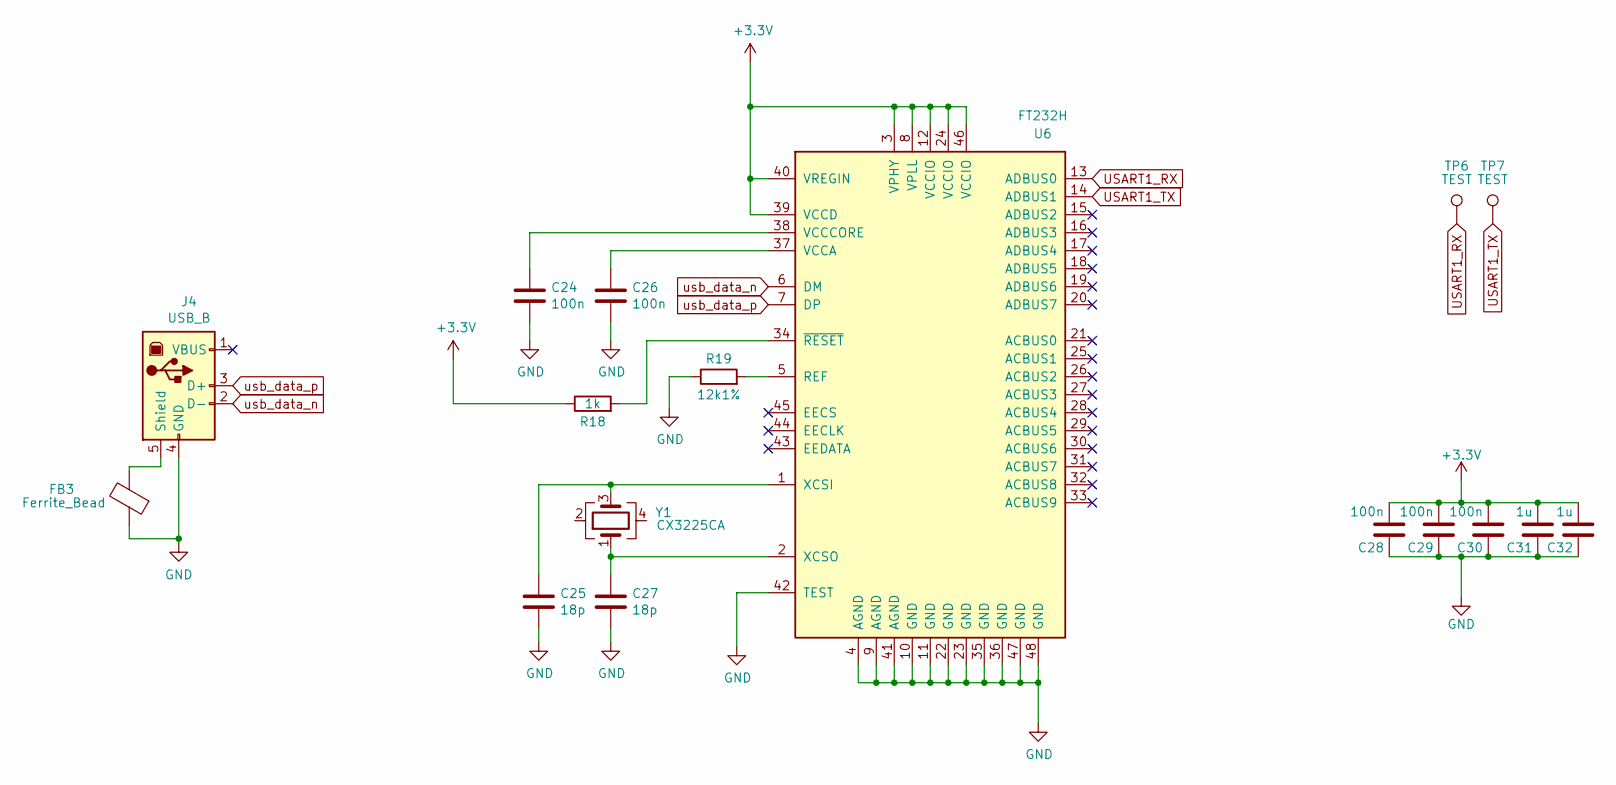
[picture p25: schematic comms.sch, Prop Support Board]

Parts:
C24, C26, C28, C29, C30: 100n; C_0805_2012Metric
C25, C27: 18p; C_0805_2012Metric
C31, C32: 1u; C_1206_3216Metric
FB3: Ferrite_Bead; R_1206_3216Metric
J4: USB_B; USB_B_OST_USB-B1HSxx_Horizontal
R18: 1k; R_0805_2012Metric
R19: 12k1%; R_0805_2012Metric
TP6, TP7: TEST; TestPoint_THTPad_D1.0mm_Drill0.5mm
U6: FT232H; LQFP-48_7x7mm
Y1: CX3225CA; Crystal_SMD_3225-4Pin_3.2x2.5mm

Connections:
+3V3: C28.2, C29.2, C30.2, C31.2, C32.2, R18.1, U6.3 (VPHY), U6.8 (VPLL), U6.12 (VCCIO), U6.24 (VCCIO), U6.39 (VCCD), U6.40 (VREGIN), U6.46 (VCCIO); also elsewhere on the board
GND: C24.2, C25.2, C26.2, C27.2, C28.1, C29.1, C30.1, C31.1, C32.1, FB3.1, J4.4 (GND), R19.1, U6.4 (AGND), U6.9 (AGND), U6.10 (GND), U6.11 (GND), U6.22 (GND), U6.23 (GND), U6.35 (GND), U6.36 (GND), U6.41 (AGND), U6.42 (TEST), U6.47 (GND), U6.48 (GND); also elsewhere on the board
unnamed: C24.1, U6.38 (VCCCORE)
unnamed: C25.1, U6.1 (XCSI), Y1.3
unnamed: C26.1, U6.37 (VCCA)
unnamed: C27.1, U6.2 (XCSO), Y1.1
unnamed: FB3.2, J4.5 (Shield)
unnamed: R18.2, U6.34 (~RESET)
unnamed: R19.2, U6.5 (REF)
USART1_RX: TP6.1, U6.13 (ADBUS0); also elsewhere on the board
USART1_TX: TP7.1, U6.14 (ADBUS1); also elsewhere on the board
usb_data_n: J4.2 (D-), U6.6 (DM)
usb_data_p: J4.3 (D+), U6.7 (DP)

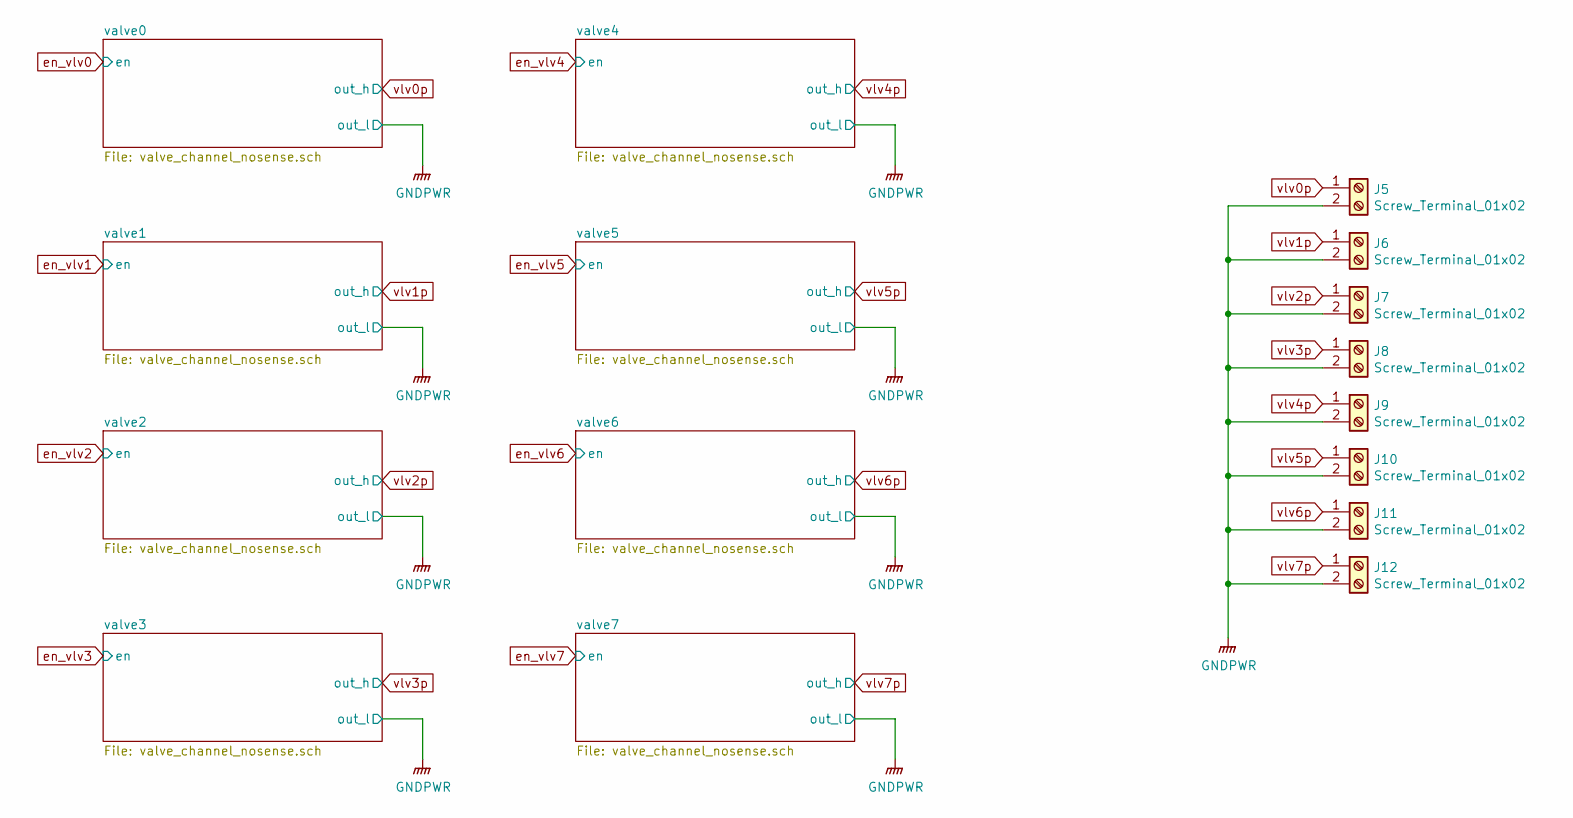
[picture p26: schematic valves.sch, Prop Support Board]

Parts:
J5, J6, J7, J8, J9, J10, J11, J12: Screw_Terminal_01x02; PhoenixContact_MSTBVA_2,5_2-G_1x02_P5.00mm_Vertical

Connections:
GNDPWR: J5.2, J6.2, J7.2, J8.2, J9.2, J10.2, J11.2, J12.2; also elsewhere on the board
vlv0p: J5.1; also elsewhere on the board
vlv1p: J6.1; also elsewhere on the board
vlv2p: J7.1; also elsewhere on the board
vlv3p: J8.1; also elsewhere on the board
vlv4p: J9.1; also elsewhere on the board
vlv5p: J10.1; also elsewhere on the board
vlv6p: J11.1; also elsewhere on the board
vlv7p: J12.1; also elsewhere on the board

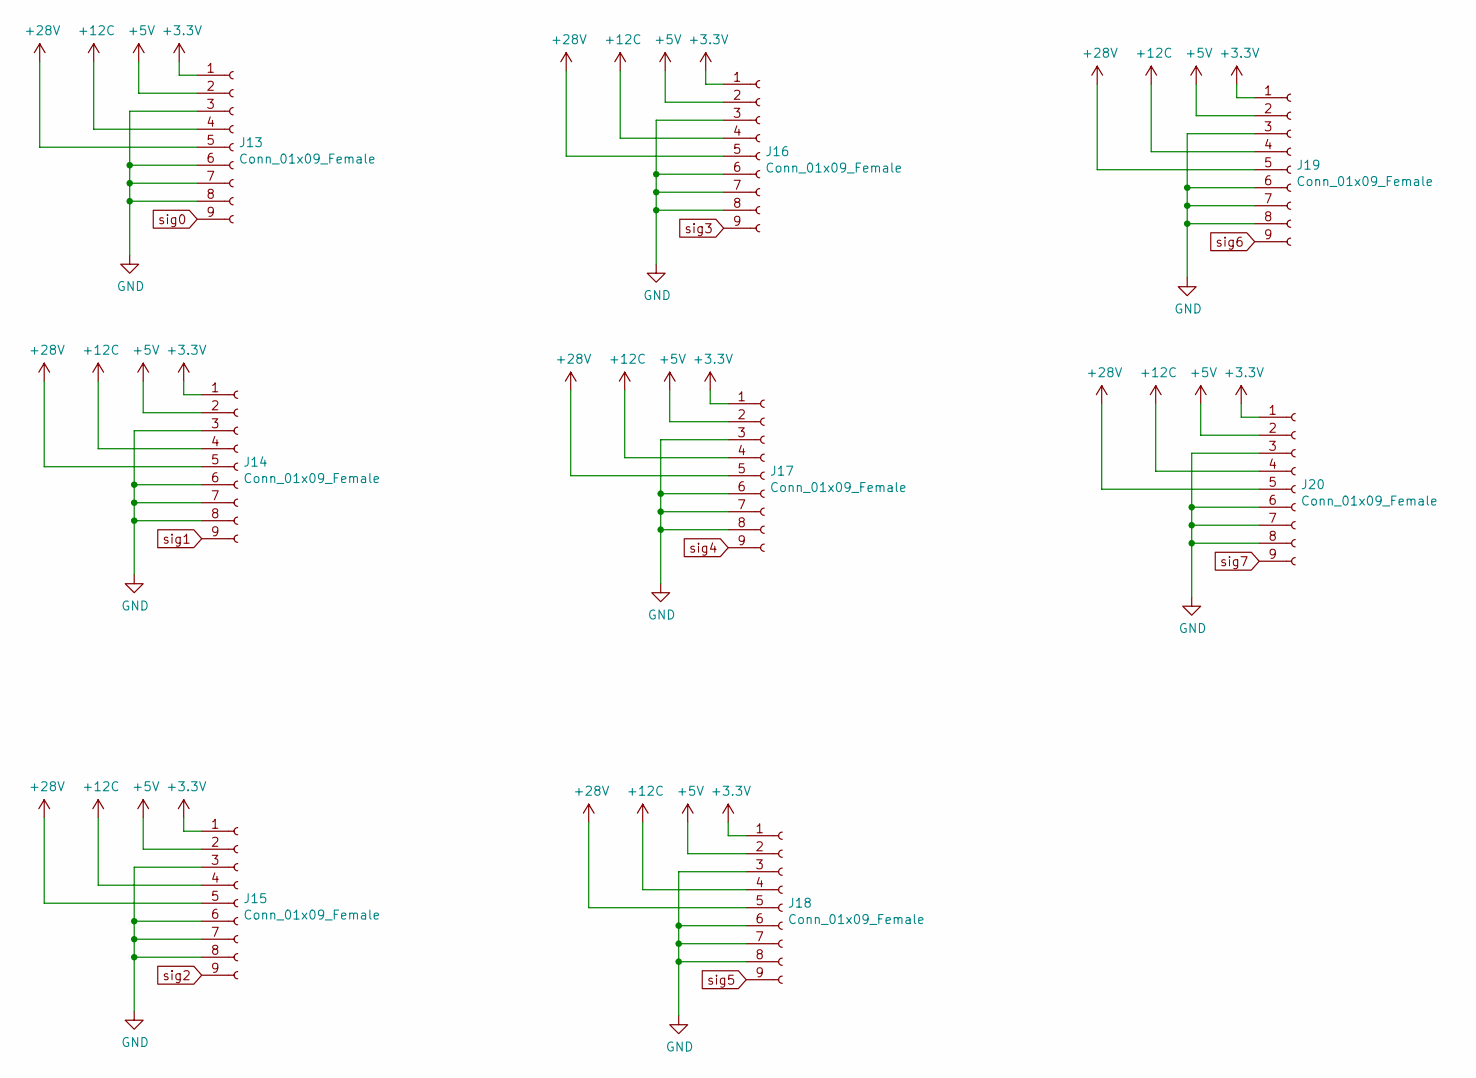
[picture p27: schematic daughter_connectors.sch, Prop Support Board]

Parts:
J13, J14, J15, J16, J17, J18, J19, J20: Conn_01x09_Female; DaughterBoardConnector

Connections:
+3V3: J13.1, J14.1, J15.1, J16.1, J17.1, J18.1, J19.1, J20.1; also elsewhere on the board
+5V: J13.2, J14.2, J15.2, J16.2, J17.2, J18.2, J19.2, J20.2; also elsewhere on the board
+12C: J13.4, J14.4, J15.4, J16.4, J17.4, J18.4, J19.4, J20.4; also elsewhere on the board
+28V: J13.5, J14.5, J15.5, J16.5, J17.5, J18.5, J19.5, J20.5; also elsewhere on the board
GND: J13.3, J13.6, J13.7, J13.8, J14.3, J14.6, J14.7, J14.8, J15.3, J15.6, J15.7, J15.8, J16.3, J16.6, J16.7, J16.8, J17.3, J17.6, J17.7, J17.8, J18.3, J18.6, J18.7, J18.8, J19.3, J19.6, J19.7, J19.8, J20.3, J20.6, J20.7, J20.8; also elsewhere on the board
sig0: J13.9; also elsewhere on the board
sig1: J14.9; also elsewhere on the board
sig2: J15.9; also elsewhere on the board
sig3: J16.9; also elsewhere on the board
sig4: J17.9; also elsewhere on the board
sig5: J18.9; also elsewhere on the board
sig6: J19.9; also elsewhere on the board
sig7: J20.9; also elsewhere on the board

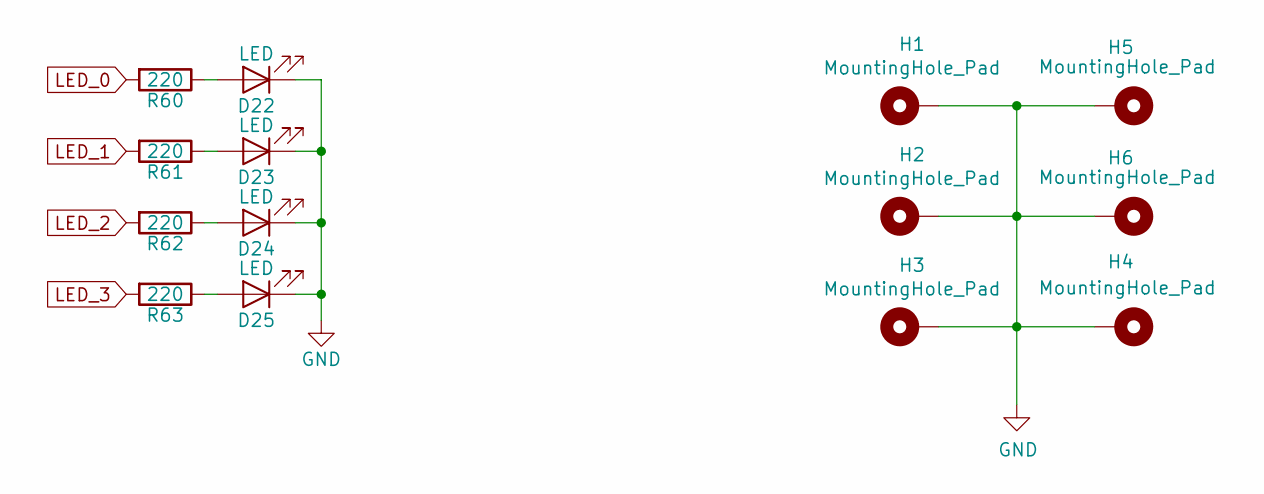
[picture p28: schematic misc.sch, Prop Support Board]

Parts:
D22, D23, D24, D25: LED; LED_0805_2012Metric
H1, H2, H3, H4, H5, H6: MountingHole_Pad; MountingHole_3.2mm_M3_Pad
R60, R61, R62, R63: 220; R_0805_2012Metric

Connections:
GND: D22.1 (K), D23.1 (K), D24.1 (K), D25.1 (K), H1.1, H2.1, H3.1, H4.1, H5.1, H6.1; also elsewhere on the board
LED_0: R60.2; also elsewhere on the board
LED_1: R61.2; also elsewhere on the board
LED_2: R62.2; also elsewhere on the board
LED_3: R63.2; also elsewhere on the board
unnamed: D22.2 (A), R60.1
unnamed: D23.2 (A), R61.1
unnamed: D24.2 (A), R62.1
unnamed: D25.2 (A), R63.1

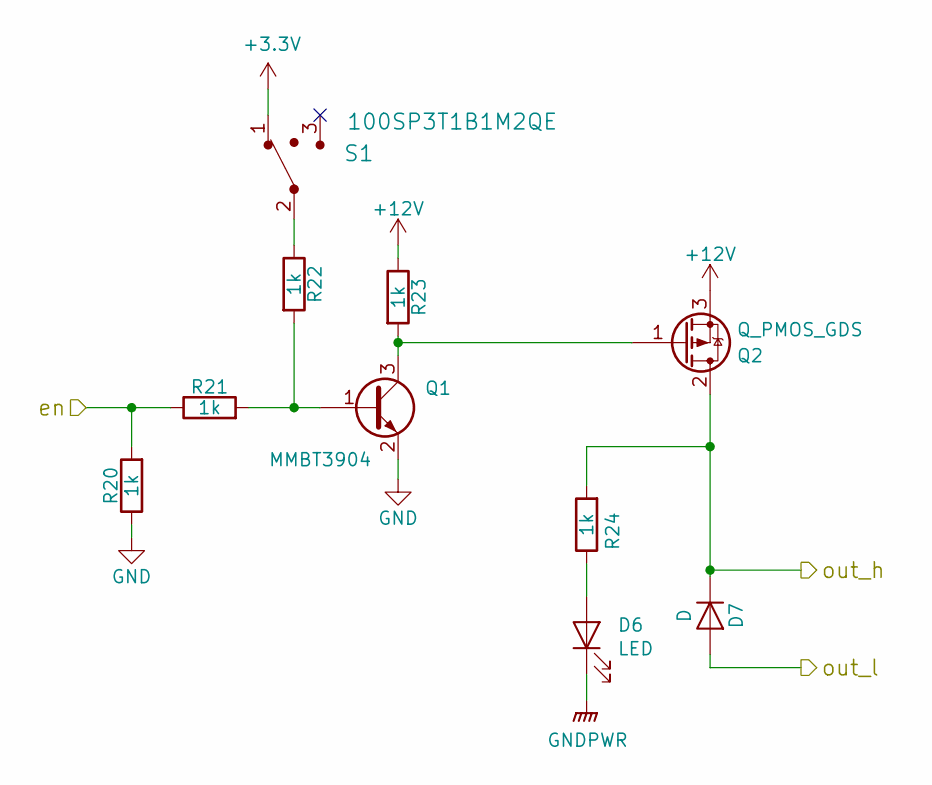
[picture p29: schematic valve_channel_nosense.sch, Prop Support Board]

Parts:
D6: LED; LED_0805_2012Metric
D7: D; SODFL4725X110N
Q1: MMBT3904; SOT-23
Q2: Q_PMOS_GDS; TO-252-2
R20, R21, R22, R23, R24: 1k; R_0805_2012Metric
S1: 100SP3T1B1M2QE; Toggle_Switch_100SP1T1B4M2QE; Digi-Key_PN EG2355-ND

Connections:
+3V3: S1.1; also elsewhere on the board
+12V: Q2.3 (S), R23.1; also elsewhere on the board
GND: Q1.2 (E), R20.1; also elsewhere on the board
GNDPWR: D6.1 (K), D7.2 (A); also elsewhere on the board
unnamed: D6.2 (A), R24.1
unnamed: Q1.1 (B), R21.2, R22.2
unnamed: Q1.3 (C), Q2.1 (G), R23.2
unnamed: R22.1, S1.2 (Com)
en_vlv0: R20.2, R21.1; also elsewhere on the board
vlv0p: D7.1 (K), Q2.2 (D), R24.2; also elsewhere on the board

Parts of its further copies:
D8, D10, D12, D14, D16, D18, D20: LED; LED_0805_2012Metric
D9, D11, D13, D15, D17, D19, D21: D; SODFL4725X110N
Q3, Q5, Q7, Q9, Q11, Q13, Q15: MMBT3904; SOT-23
Q4, Q6, Q8, Q10, Q12, Q14, Q16: Q_PMOS_GDS; TO-252-2
R25, R26, R27, R28, R29, R30, R31, R32, R33, R34, R35, R36, R37, R38, R39, R40, R41, R42, R43, R44, R45, R46, R47, R48, R49, R50, R51, R52, R53, R54, R55, R56, R57, R58, R59: 1k; R_0805_2012Metric
S2, S3, S4, S5, S6, S7, S8: 100SP3T1B1M2QE; Toggle_Switch_100SP1T1B4M2QE; Digi-Key_PN EG2355-ND

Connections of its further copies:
+3V3: S2.1, S3.1, S4.1, S5.1, S6.1, S7.1, S8.1; also elsewhere on the board
+12V: Q4.3 (S), Q6.3 (S), Q8.3 (S), Q10.3 (S), Q12.3 (S), Q14.3 (S), Q16.3 (S), R28.1, R33.1, R38.1, R43.1, R48.1, R53.1, R58.1; also elsewhere on the board
GND: Q3.2 (E), Q5.2 (E), Q7.2 (E), Q9.2 (E), Q11.2 (E), Q13.2 (E), Q15.2 (E), R25.1, R30.1, R35.1, R40.1, R45.1, R50.1, R55.1; also elsewhere on the board
GNDPWR: D8.1 (K), D9.2 (A), D10.1 (K), D11.2 (A), D12.1 (K), D13.2 (A), D14.1 (K), D15.2 (A), D16.1 (K), D17.2 (A), D18.1 (K), D19.2 (A), D20.1 (K), D21.2 (A); also elsewhere on the board
unnamed: D8.2 (A), R29.1
unnamed: D10.2 (A), R34.1
unnamed: D12.2 (A), R39.1
unnamed: D14.2 (A), R44.1
unnamed: D16.2 (A), R49.1
unnamed: D18.2 (A), R54.1
unnamed: D20.2 (A), R59.1
unnamed: Q3.1 (B), R26.2, R27.2
unnamed: Q3.3 (C), Q4.1 (G), R28.2
unnamed: Q5.1 (B), R31.2, R32.2
unnamed: Q5.3 (C), Q6.1 (G), R33.2
unnamed: Q7.1 (B), R36.2, R37.2
unnamed: Q7.3 (C), Q8.1 (G), R38.2
unnamed: Q9.1 (B), R41.2, R42.2
unnamed: Q9.3 (C), Q10.1 (G), R43.2
unnamed: Q11.1 (B), R46.2, R47.2
unnamed: Q11.3 (C), Q12.1 (G), R48.2
unnamed: Q13.1 (B), R51.2, R52.2
unnamed: Q13.3 (C), Q14.1 (G), R53.2
unnamed: Q15.1 (B), R56.2, R57.2
unnamed: Q15.3 (C), Q16.1 (G), R58.2
unnamed: R27.1, S2.2 (Com)
unnamed: R32.1, S3.2 (Com)
unnamed: R37.1, S4.2 (Com)
unnamed: R42.1, S5.2 (Com)
unnamed: R47.1, S6.2 (Com)
unnamed: R52.1, S7.2 (Com)
unnamed: R57.1, S8.2 (Com)
en_vlv1: R25.2, R26.1; also elsewhere on the board
en_vlv2: R30.2, R31.1; also elsewhere on the board
en_vlv3: R35.2, R36.1; also elsewhere on the board
en_vlv4: R40.2, R41.1; also elsewhere on the board
en_vlv5: R45.2, R46.1; also elsewhere on the board
en_vlv6: R50.2, R51.1; also elsewhere on the board
en_vlv7: R55.2, R56.1; also elsewhere on the board
vlv1p: D9.1 (K), Q4.2 (D), R29.2; also elsewhere on the board
vlv2p: D11.1 (K), Q6.2 (D), R34.2; also elsewhere on the board
vlv3p: D13.1 (K), Q8.2 (D), R39.2; also elsewhere on the board
vlv4p: D15.1 (K), Q10.2 (D), R44.2; also elsewhere on the board
vlv5p: D17.1 (K), Q12.2 (D), R49.2; also elsewhere on the board
vlv6p: D19.1 (K), Q14.2 (D), R54.2; also elsewhere on the board
vlv7p: D21.1 (K), Q16.2 (D), R59.2; also elsewhere on the board

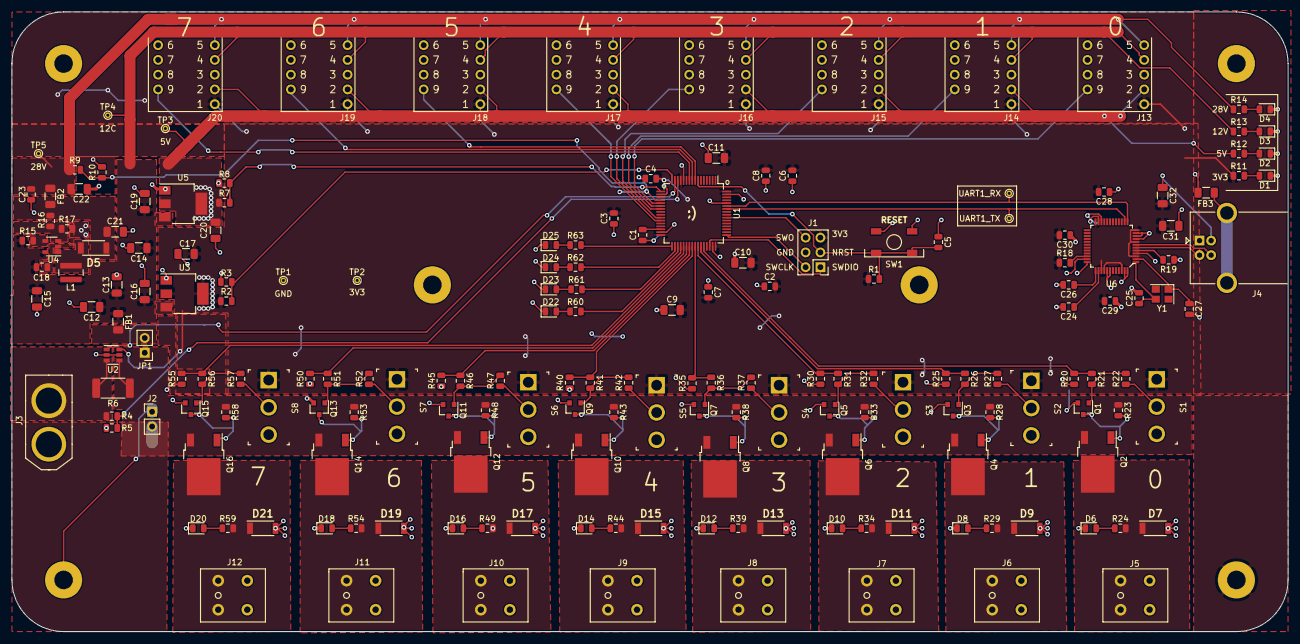
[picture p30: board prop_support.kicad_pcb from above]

Board: 2 copper layers, 219.7 x 106.7 mm, 190 parts (0 on the bottom side), 102 nets.

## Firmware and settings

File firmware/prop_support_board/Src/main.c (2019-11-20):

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

/* Includes ------------------------------------------------------------------*/
#include "main.h"

ADC_HandleTypeDef hadc1;

UART_HandleTypeDef huart1;

void SystemClock_Config(void);
static void MX_GPIO_Init(void);
static void MX_ADC1_Init(void);
static void MX_USART1_UART_Init(void);
/**
  * @brief  The application entry point.
  * @retval int
  */
int main(void)
{
  /* MCU Configuration--------------------------------------------------------*/

  /* Reset of all peripherals, Initializes the Flash interface and the Systick. */
  HAL_Init();

  /* Configure the system clock */
  SystemClock_Config();

  /* Initialize all configured peripherals */
  MX_GPIO_Init();
  MX_ADC1_Init();
  MX_USART1_UART_Init();
  /* Infinite loop */
  /* USER CODE BEGIN WHILE */
  while (1)
  {
    /* USER CODE END WHILE */

    /* USER CODE BEGIN 3 */
	  uint16_t delay = 200;
	  GPIO_TypeDef* led_ports[4] = {led0_GPIO_Port, led1_GPIO_Port, led2_GPIO_Port, led3_GPIO_Port};
	  uint16_t led_pins[4] = {led0_Pin, led1_Pin, led2_Pin, led3_Pin};
	  HAL_GPIO_WritePin(en_vlv0_Pin, en_vlv0_GPIO_Port, GPIO_PIN_SET);
	  HAL_GPIO_WritePin(en_vlv1_Pin, en_vlv1_GPIO_Port, GPIO_PIN_SET);
	  HAL_GPIO_WritePin(en_vlv2_Pin, en_vlv2_GPIO_Port, GPIO_PIN_SET);
	  HAL_GPIO_WritePin(en_vlv3_Pin, en_vlv3_GPIO_Port, GPIO_PIN_SET);
	  HAL_GPIO_WritePin(en_vlv4_Pin, en_vlv4_GPIO_Port, GPIO_PIN_SET);
	  HAL_GPIO_WritePin(en_vlv5_Pin, en_vlv5_GPIO_Port, GPIO_PIN_SET);
	  HAL_GPIO_WritePin(en_vlv6_Pin, en_vlv6_GPIO_Port, GPIO_PIN_SET);
	  HAL_GPIO_WritePin(en_vlv7_Pin, en_vlv7_GPIO_Port, GPIO_PIN_SET);
	  for(int i=0; i<=3; i++){
		  HAL_GPIO_WritePin(led_ports[i], led_pins[i], GPIO_PIN_SET);
		  HAL_Delay(delay);
	  }
	  for(int i=0; i<=3; i++){
	  		  HAL_GPIO_WritePin(led_ports[i], led_pins[i], GPIO_PIN_RESET);
	  		  HAL_Delay(delay);
	  }

  }
  /* USER CODE END 3 */
}

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


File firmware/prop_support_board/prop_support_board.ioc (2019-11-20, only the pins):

Mcu.UserName=STM32F446RETx
PA0-WKUP.Signal=ADCx_IN0
PA1.Signal=ADCx_IN1
PA10.GPIO_Label=en_vlv1
PA10.Signal=GPIO_Output
PA11.GPIO_Label=en_vlv0
PA11.Signal=GPIO_Output
PA13.Signal=SYS_JTMS-SWDIO
PA14.Signal=SYS_JTCK-SWCLK
PA2.Signal=ADCx_IN2
PA3.Signal=ADCx_IN3
PA4.Signal=ADCx_IN4
PA5.Signal=ADCx_IN5
PA6.Signal=ADCx_IN6
PA7.Signal=ADCx_IN7
PA8.GPIO_Label=en_vlv3
PA8.Signal=GPIO_Output
PA9.GPIO_Label=en_vlv2
PA9.Signal=GPIO_Output
PB0.Signal=ADCx_IN8
PB1.Signal=ADCx_IN9
PB12.GPIO_Label=led3
PB12.Signal=GPIO_Output
PB13.GPIO_Label=led2
PB13.Signal=GPIO_Output
PB14.GPIO_Label=led1
PB14.Signal=GPIO_Output
PB15.GPIO_Label=led0
PB15.Signal=GPIO_Output
PB3.Signal=SYS_JTDO-SWO
PB6.Signal=USART1_TX
PB7.Signal=USART1_RX
PC0.Signal=ADCx_IN10
PC1.Signal=ADCx_IN11
PC2.Signal=ADCx_IN12
PC6.GPIO_Label=en_vlv7
PC6.Signal=GPIO_Output
PC7.GPIO_Label=en_vlv6
PC7.Signal=GPIO_Output
PC8.GPIO_Label=en_vlv5
PC8.Signal=GPIO_Output
PC9.GPIO_Label=en_vlv4
PC9.Signal=GPIO_Output

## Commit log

2019-04-03 added daughter board kicad projects
    [3wireducer_daughter.kicad_pcb, 3wireducer_daughter.sch, 4wireducer_daughter.kicad_pcb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]
2019-04-04 3 boards down...
    [3wireducer_daughter-B_Cu.gbl, 3wireducer_daughter-B_Mask.gbs, 3wireducer_daughter-B_SilkS.gbo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]
2019-04-09 first MX export
    [3wireducer_daughter.sch, comms.sch, loadcell_daughter.sch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]
2019-04-09 Updated Master Sheet
    [Prop Support Board REV A Mastersheet.xlsx, prop_support_bom.csv]
2019-04-09 gui copied from nsternie/live_telemetry
    Copied over some of my previous work from the live telem project as a framework for this gui
    [Prop Support Board REV A Mastersheet.xlsx, graph_settings.csv]
2019-09-13 push for jack
    [Prop Support Board REV A Mastersheet.xlsx, prop_support.kicad_pcb, psb_pcb.iges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]
2019-11-20 port project to STM32CubeIDE

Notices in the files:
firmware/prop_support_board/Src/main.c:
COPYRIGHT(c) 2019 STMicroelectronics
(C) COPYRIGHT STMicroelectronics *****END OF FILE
